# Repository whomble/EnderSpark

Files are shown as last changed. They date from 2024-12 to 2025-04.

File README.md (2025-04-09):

# WireEDM

Wire EDM uses electrical discharges to cut any conductive materials (brass, steel, aluminium even tungsten carbide) with no mechanical forces, enabling high precision, deep cuts, and machining of hard or delicate materials without deformation. 
This project demonstrates how to build a DIY wire EDM machine using salvaged components from an old 3D printer and other affordable parts, keeping the total cost around 250€ + 4 machined parts the ender 3 and less than 50h of work.

The machine's frame and motion system leverage the hardware of the Ender 3,  with 1:51 gear reductions on the X and Y axes to enable extremely slow and precise movements required for EDM. 
A Raspberry Pi Pico clone with a TC4428 and a powerful MOSFET are used to switch up to 10A at 50KHz

This project includes guidance on generating toolpaths using a modified post processor from Fusion 360
Depending on the availability of tools and salvaged materials, replication costs may vary slightly. This project took me a few hundreds of hours of developpment but you should be able to replicate in less than 50h.

The conversion from a 3D printer to a wire EDM can be done in 6 steps:
- Mechanical modifications
- Wire feeder
- Firmware update (marlin)
- Ark generator
- Water loop
- Fusion 360 post processor

The full part list with some product links is in the [parts folder](Parts/)

# WARNiNGS
The voltage is lower than the SELV (50V for AC 120V for DC) in DRY CONDITIONS, for WET CONDITION the SELV is (25V for AC and 60 for DC). In addition there is no GFCI to protect you so disconnect the PSU everytime you're planning to touch a metalic component and wear at leat nitrile gloves. If you don't know precisely what you are doing just skip this project.

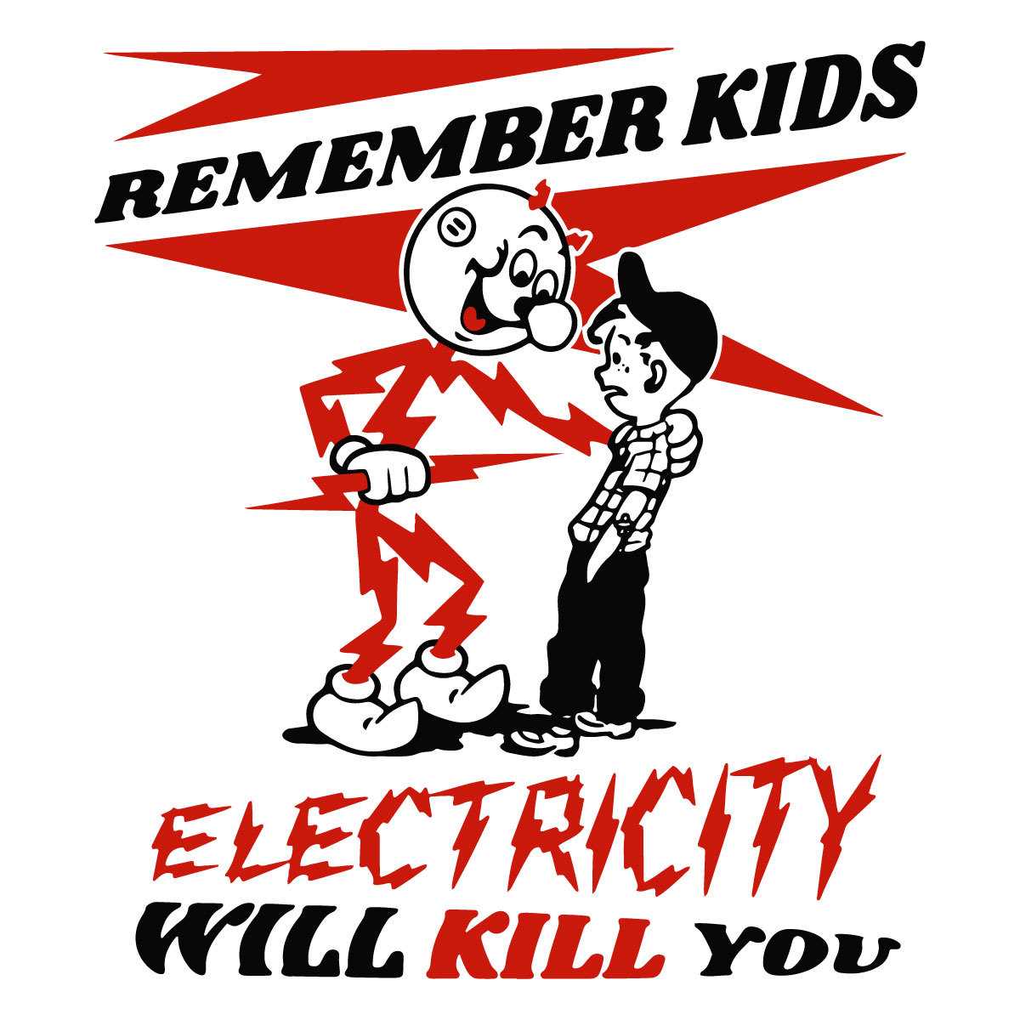
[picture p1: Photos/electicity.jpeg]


Copper is considered as a heavy metal, the best way to deal with the dirty water is to let it sit for a while in a ventilated area to evaporate all the water, after that it's jsut metal powder and can be disposed in the local recycling center.

# Mecanical parts
## Motion

A big advantage of wire EDM compared to CNC milling is that the frame doesn't need to be very stiff, the hardware just need to support the wire feeder on the X axis and the water tank ~4kg on the Y axis. The Z axis isn't used during the cutting process but it's quite usefull to help changing the wire.

I've had a linear rail (MGN12H) on X and Y axis, it can be bolted directly on X axis with T nuts and for the why axis you need to drill 4 holes in the buildplate support thats all.
Wire EDM can be very slow depending on the thickness so one of the most important requirement is to be able to move slowly at a fixed rate. Regular stepper motors aren't able to do that, even with microstepping I made a fully printable belt reducer 1:64 but it need some improvements so I've just brought gearbox for nema 17 that can be directly connected to a 2GT pulley.

## Wire feeder

The wire feeder is the only complicated part which need to be custom made because it needs to fullfill a few requierments:
- Stifness, during the cutting process the arcs can generate vibrations, to achieve a good surface finish the wire need to be very straight
- Electrically insulated, even if the cutting is done under de-ionised water some electrolysis can occur which can reduce the power output. An insulated feeder also prevent from shorts if a metal part fall between the wire and the feeder
- Grounded, at 20kHz the long wire is a big antenna which can emit a lot of parasites and damage electronics. Grounding as much part as possible is crucial to avoid that (and any risk for pacemaker users)
- Tensionner mechanism, to avoid wire vibration the wire need to be adequatly tensionned.
- Waste spool, wire edm consume the workpiece AND the wire, depending on the material it can use a lot of wire
- Hard wire guide, I you have an old ender 3 you've probably experience filament grinding the extruder even if its plastic against plastic, the same thing can happend here with soft brass

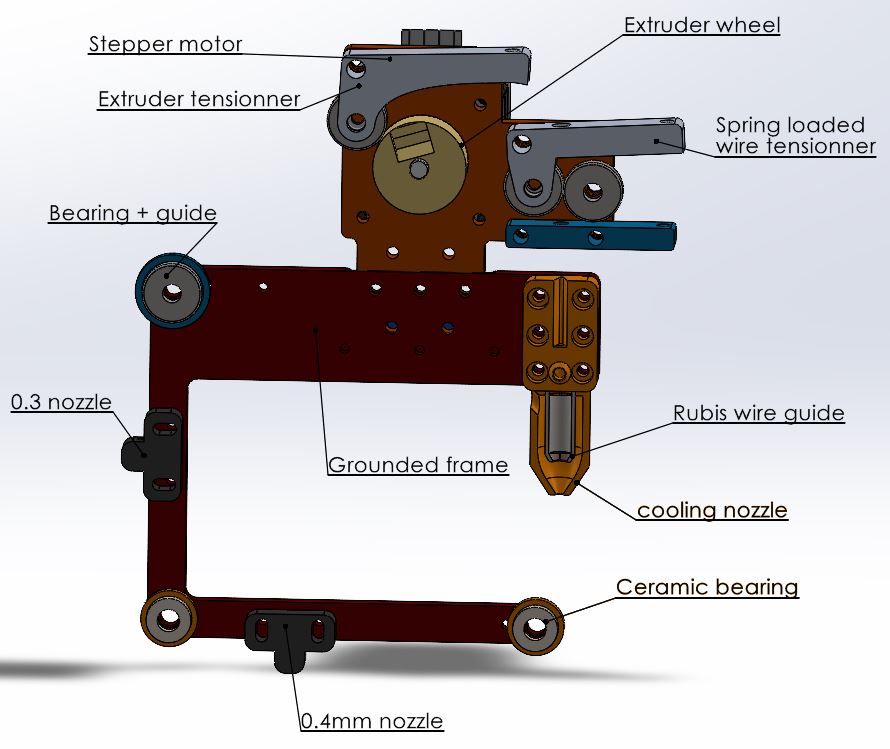
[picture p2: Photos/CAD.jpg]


This is the CAD of the second version, the extruder (nema 17 + a brass cylinder) is pulling the wire all the way from the tensionner. 
The tensionner conssit of two all bearing pressing into each other like a 3D printer extruder, the sping can b adjust to block more the wire and provide more tension.
Then, the wire need to be guided very precisely, for the upper guide I use a off the shelf rubis nozzle with a plastic nozzle around it for watercooling. The lower guide is a ceramic ball bearing with a PLA spacer and a .4mm brass nozzle to push the wire against the spacer. The two other ball bearings (ceramic for the lower one and steel with plastic cover for the upper one) just guide the wire to the extruder.

The ball bearings needs to be in ceramic for three reason:
1. Corosion
2. No lubricant can desovle in water
3. High hardness

The wire is connected to the (-) terminal of the PSU by the brass wheel and in the future a tungsten carbide contact block, but since the wire emit EMF like an antenna, I want to ground as much metal as I can, so the whole motor assembly is at the same potential as the wire, but the frame of the printer and the red part are grounded. The voltage arent high so a layer of epoxy or an anodization is enougth to insulate the two regions.

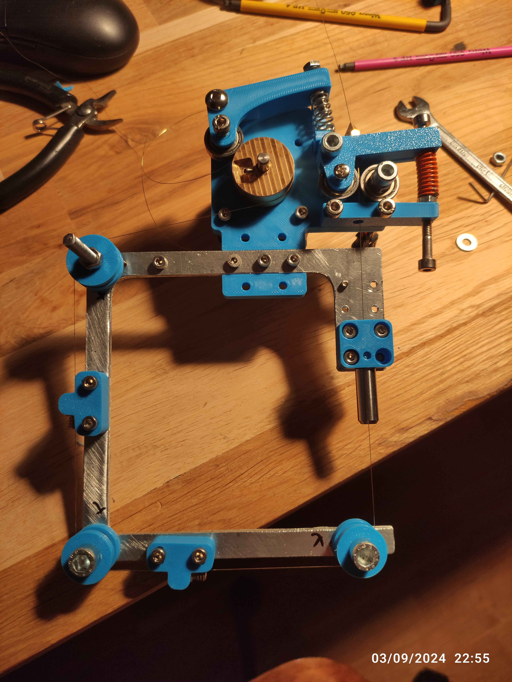
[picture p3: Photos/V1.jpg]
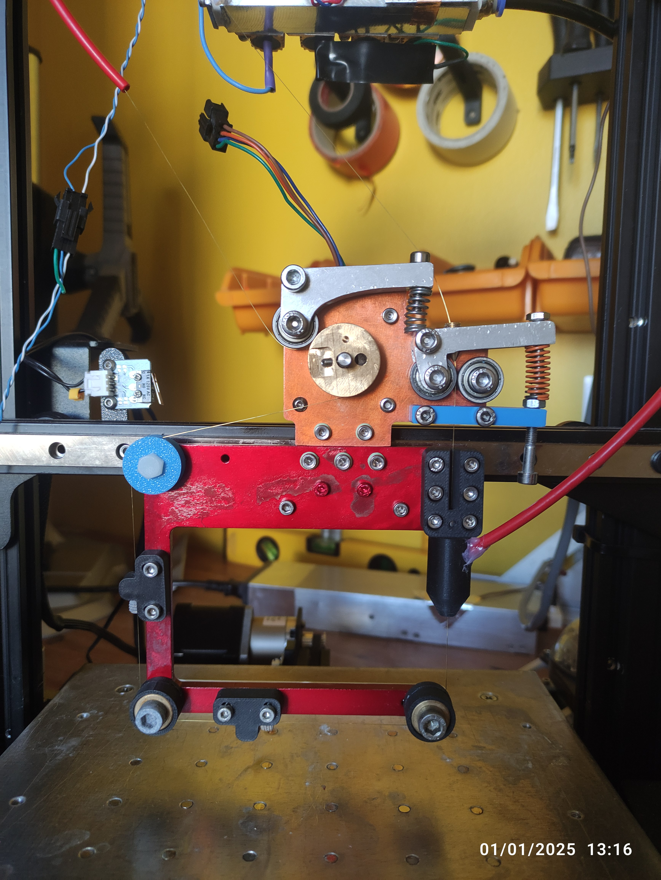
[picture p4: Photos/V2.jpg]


The first version on the left use a lots of printed parts, it works but the tensionner some part can flex and reduce the wire tension/straightness so I made a second version in 5mm thick alluminium plate with 10mm thick tensionners.

All the parts are availlable in .sldprt and .step

### Manufcaturing

Both the red and orange parts are 5mm thick aluminium cutted with my homemade CNC with a 3.175mm single flute endmill, the geometry is a bit complex and can be improve but if you want to make it there is a catch. The two parts are electrically insulated and need to be very straight, there is two options for insulating metalic coating. 
- Anodisation of aluminium + galvanic varnish, it requier sulfuric acid and other chemicals and it's not that easy to make a thick and strong coating
- Powder coating, there's a few hobbist projects but it involve fine powder which isn't better than sulfuric acid.

Both can be DIY or manufacturer by a chinese company like pcbway or whatever, in the case of powder coating, the frame can be made out of steel (not stainless) wich will give way more stifness. 

The two other aluminium parts doesn't need any coating same for the brass wheel, it's just a cylinder with 3 holes.

### Spool

Wire edm as you can guess consume wire, so I need a simple way to manage the waste wire. My solution is to have the new spool of wireconnected to the waste spool with magnet so the second one can be drived by the first one. Since the first spool will get smaller and smaller and the second bigger and bigger, the first one will have to turn way fater to maintain a tension. With this configurtion, the first spool has a way smaller inner diameter which made it spin fzster at any moment. The magnets act like a clutch to maintain constant load at variable speeds.

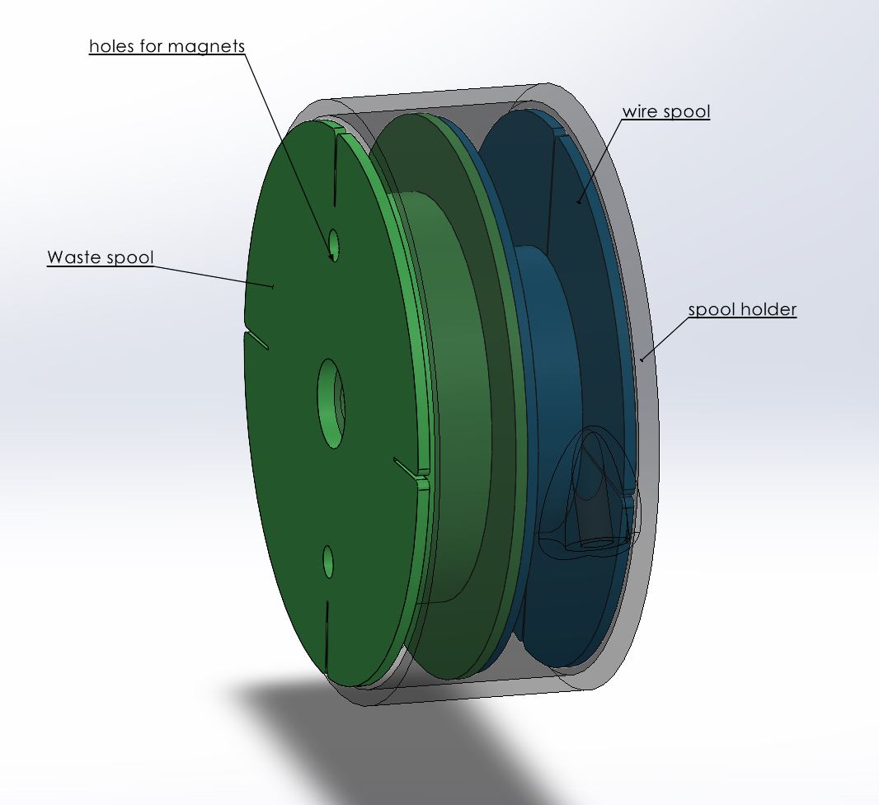
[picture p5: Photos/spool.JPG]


# Electronics
## generator

It's actually pretty easy to make an arc for EDM, it won't be as powerfull as a commercial machine but pretty close. We just need to switch a powerfull MOSFET on and of very fast, I use the IRF135B203 wich can handle 135V 129A and 500A peak. The mosfet is drived by a TC4428 with a schotcky diode to protect the IC a square pwm signal is generated by the pi pico, the pico code is optimised to generate the wave as fast as possible.



## Power managment 

The power supply should be able to deliver at least 5A, 48V is enougth to cutt alluminium but a higher voltager means a higher energy stored in the capacitors (E = 1/2C U²). If you plan to cut copper or steel you can buy a switch mode power supply with adjustable output (mine can go up to 110V).

In the best case scenario, each pulse will create an arc and remove some matter but in realitty sometimes the wire is too far to create a spark and sometimes the wir eis in direct contact and will create a (momentary) short circuit. In the future I will make a short circuit detection system but for now a serie of 100W what resistors limit the current to avoid destroing the PSU and the wire.

Last part is the capacitors, it helps deliver high current durring short amount of time. You can't use some standard electrolitic capacitor (belive me I tried) ceramic is a good option but we need very low ESR so polymer is the only suitable option. In my setup I use 4x 4.7uF in parallel so ~20uF rated for 200V.

These 3 main components are connected to a waterblock for cooling, in my experience it's a bit overkilled and air cooling will be enougth in the future but I need to circulate the water anyway so...

# Water

The EDM process must be done under a dielectric fluid, it can be ethanol, oil or kerosene but the easyest solution is obviously deionised water. Water is also used for cooling (the electrical components and the workpiece) and chip evacuation. The "builtplate" is a water tank made out of acrily sheets welded with aceton and a bit of silicone for etancheity. I've also add a steel shit so I can quickly remove it from my magnetic buildplate.

EDM generate a ton of small metalic particles which needs to be filter during the cutting, The best pump I've found is a membrane pump which can provide high pressure (necessary for good filtration) and is quite silent when underpowered, it's design for 24V and I power it between 5-7V depending on the material. The filter is a standard polyester coton filter <0.1um in a cardrige in the future I'll probably try washables filters like ceramic or stainless steel. I use push pull and 6mm tubes for all my connection except for the nozzle its a 4mm.

After each cuts I put the deionised water in it's original tank for decantation, and separate the "pure" water from the dirty one a few days later.

Copper is consiered as a heavy metal, the best way to deal with the dirty water is to let it sit for a while in a ventilated area to evaporate all the water, after that it's jsut metal powder and can be disposed in the local recycling center.

# Firmware modifications

# Toolpath generation

The two easiest ways to generate a gcode is with a slicer or with a cam plugin. I've tried kirimoto which have a wire edm mode but there's very little features and you can't control the extruder. I've also tried cura, the limitation is that you can't set a very small speed, I even tried modifiyng the software but I coulnd'nt find a solution, maybe with orca slicer?

In my opinion the easyest solution is to use the CAM part of fusion 360 with the laser/waterjet mod. 



It's easy to setup a waterjet tool with 0.3mm stream and you can add a very long lead in to enter the workpiece from anywhere. You don't have to worry about feeds and speeds here, you just need to set all the hight to zero to avoid Z movements, and set up the appropriate thickness.

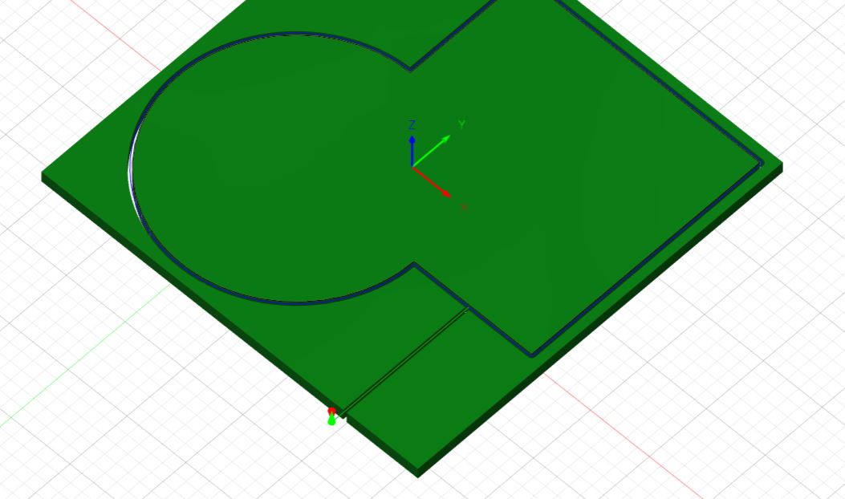
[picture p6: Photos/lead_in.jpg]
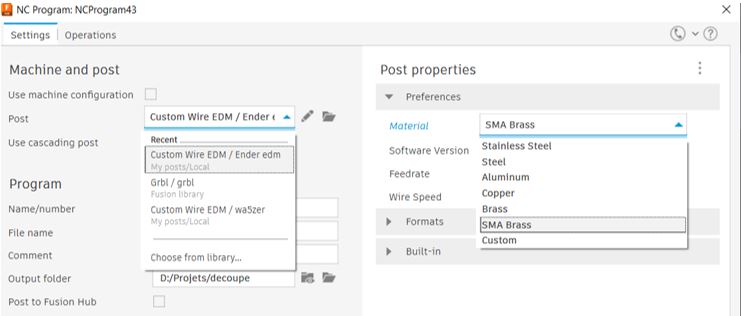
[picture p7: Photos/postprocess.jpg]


Then you need to select the wire edm post processor, I modified the wazer post processor to match my needs, I will not detail it here, the file is in this folder, you just have to paste it in the appropriate location.

I have a very small database for differents materials, so if the thickness is right, just selec the material and it should be good to go. It's an ongoing project soyou will probably have sligly differents settings than me, I'll recommand you to do a speedtest for the material you're planing to cut and modify the database:

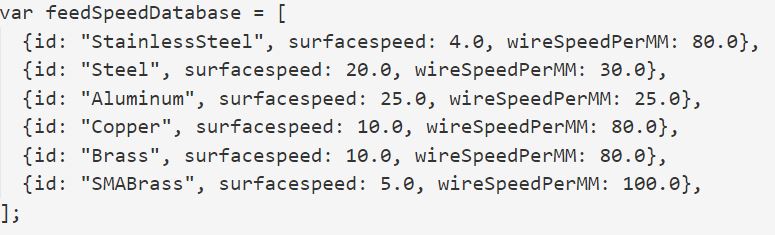
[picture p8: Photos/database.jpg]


surfacespeed is the speed in mm²/min, which correspond to the linear speed for a defined thickness ex: 3mm/min for 10mm thick aluminium is 30mm²/min.
wirespeedpermm is the wire consumed per mm² with the previous example of 30mm²/min and 25mm it will consume 750mm of wire to cut this amount of material in 1min.

A cheap 100m of 0.2mm joaillery brass wire (2€) will last for more than two hours ~0.02€/m, a more expensive 5kg of edm 0.25mm brass wire (110€) is almost 12km so ~0.01€/m and 250h of use.
In the future I will try molybdenum wire which is just a bit more expensive but it can be used several times but I need to design a back and forth drive.

Some more commun supply are also needed like heat shrink tube, solder, wires (I use wires from old RJ45 cable it can handle something like 5A without a problem, its free nd easly accessible).

A lots of tools are needed to work properly:

- Soldering iron
- Drill press
- Caliper
- Dial indicator
- Heat gun
- A good square rule
- Handed metal saw 
- Metal band saw (if your alumiun extrusions needed to be with a perfect 90° angle)
- Hand drill
- Center punch
- Marker for metal
- Hammer, clamps, screw drivers others hand tools
- 3D printer
- deburr tool

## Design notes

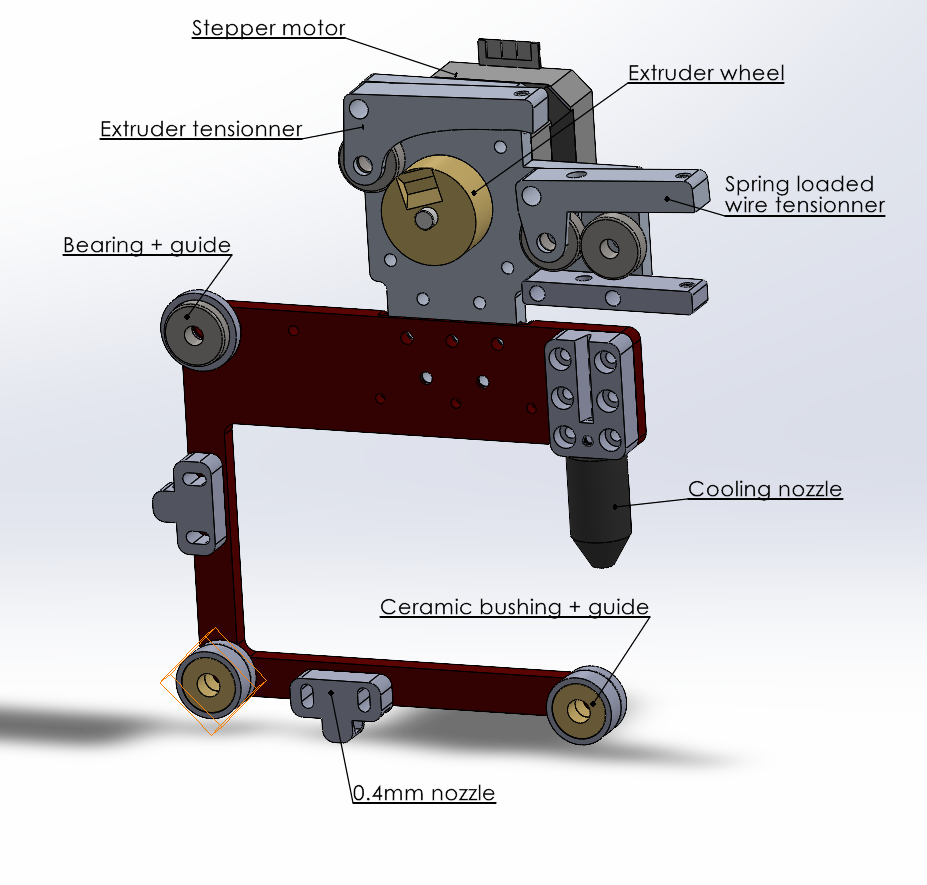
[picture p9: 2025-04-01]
Photos/wirefeeder.png

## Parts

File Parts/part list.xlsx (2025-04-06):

Raspberry pi pico | 1 | 5.0 € | 5 € | https://fr.aliexpress.com/item/1005008244091735.html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
Linear rail MGN12H 300mm | 2 | 12.0 € | 24 € | https://fr.aliexpress.com/item/1005003696820721.html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
M3*8 screws | 50 | 2.0 € | 2 € | https://fr.aliexpress.com/item/32810872544.html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
M3 T nuts | 20 | 3.0 € | 0 € | https://fr.aliexpress.com/item/32788058829.html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
M5*16 screws | 8 | 2.0 € | 2 € | https://fr.aliexpress.com/item/1005005879037174.html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
M6*12 screws | 2 | 3.0 € | 6 €
M4*12 screws | 5 | 2.0 € | 10 €
Nema 17 gearbox 1:51 | 2 | 20.0 € | 40 € | https://fr.aliexpress.com/item/1005008063969593.html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
24V membrane pump | 1 | 15.0 € | 15 € | https://fr.aliexpress.com/item/1005008493661821.html?scm_id=1007.40050.354490.0&scm-url=1007.40050.354490.0
Filter cardridge | 4 | 2.0 € | 8 € | https://fr.aliexpress.com/item/1005006706760484.html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
Filter holder | 1 | 15.0 € | 15 € | https://fr.aliexpress.com/item/1005007179471330.html?scm_id=1007.40050.354490.0&scm-url=1007.40050.354490.0
Adapter 1/2-> 6mm | 2 | 2.0 € | 4 € | https://fr.aliexpress.com/item/1005002505807954.html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
Adapter m6-> 6mm | 5 | 1.0 € | 5 €
6mm pneumatic pipes (2m) | 1 | 2.5 € | 2.5 € | https://fr.aliexpress.com/item/1005005444191688.html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
Waterblock | 1 | 8.0 € | 8 € | https://fr.aliexpress.com/item/1005004478886659.html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
TC4428 | 2 | 2.0 € | 4 € | https://fr.aliexpress.com/item/1005006912580387.html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
IRF135B203 (or similar) | 2 | 5.0 € | 10 €
4.7uF polymer capacitor | 10 | 0.8 € | 8 € | https://fr.aliexpress.com/item/1005008476927781.html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
Buck converter | 1 | 2.0 € | 2 € | https://fr.aliexpress.com/item/1005001711248152.html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
Acrylic sheet (3*235*635mm) | 1 | 20.0 € | 20 € | hardware store
Oled screen | 1 | 2.5 € | 2.5 € | https://fr.aliexpress.com/item/1005004355547926.html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
L7812CV | 1 | 2.0 € | 2 € | https://fr.aliexpress.com/item/1005007531573602.html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
JST connectors | 1 | 3.0 € | 3 € | https://fr.aliexpress.com/item/1005006498660940.html?scm_id=1007.40050.354490.0&scm-url=1007.40050.354490.0
Banana connectors | 1 | 1.5 € | 1.5 € | https://fr.aliexpress.com/item/1005006400659486.html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
Wire diodes resistor | 1 | 5.0 € | 5 €
Ceramic bearings | 2 | 6.0 € | 12 € | https://fr.aliexpress.com/item/1005008350254851.html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
Bearings | 4 | 0.0 € | 0 € | from ender3 rubber wheels
PLA ~200g | 1 | 4.0 € | 4 €
Ender3 | 1 | 0.0 € | 0 €
 |  | Total | 220.5 €
0,2mm brass wire (100m) | 5 | 2.0 € | 10 € | https://fr.aliexpress.com/item/1005006203319769.html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
0,25mm brass wire (5kg) | 1 | 110.0 € | 110 € | https://fr.aliexpress.com/item/1005006169662498.html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
0,18 molybdenum wire (2km) | 1 | 40.0 € | 40 € | https://fr.aliexpress.com/item/1005008417132381.html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

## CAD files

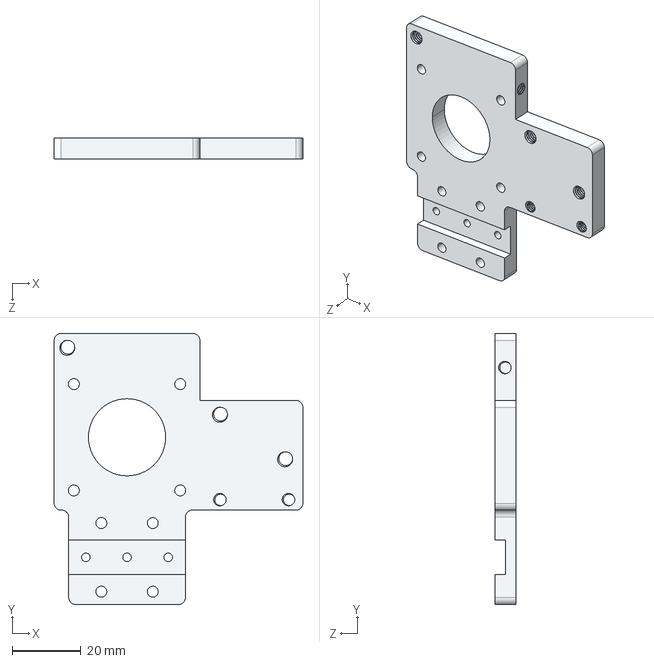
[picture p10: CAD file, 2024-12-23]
step_files/extruder mount.STEP
72.5 x 79.0 x 6.00 mm

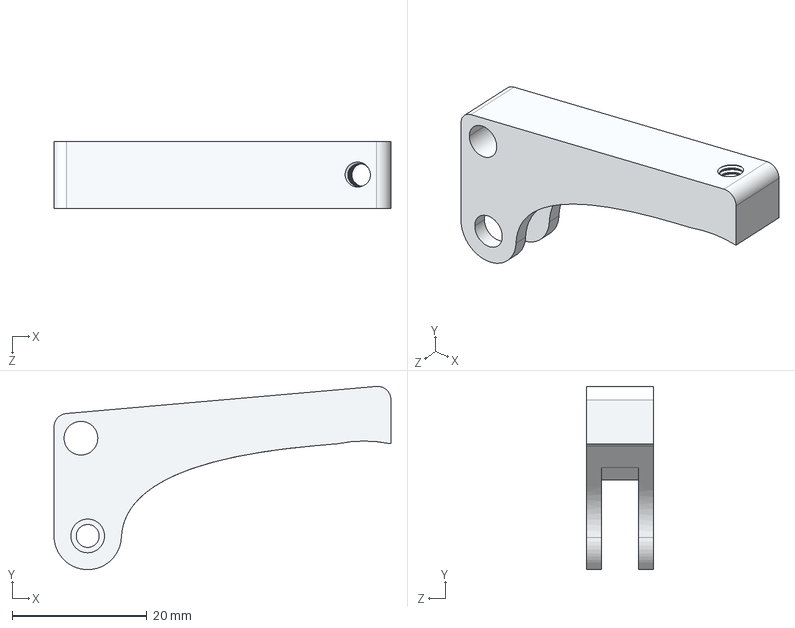
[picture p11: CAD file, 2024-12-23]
step_files/extruder tensioner.STEP
50.0 x 27.2 x 10.0 mm

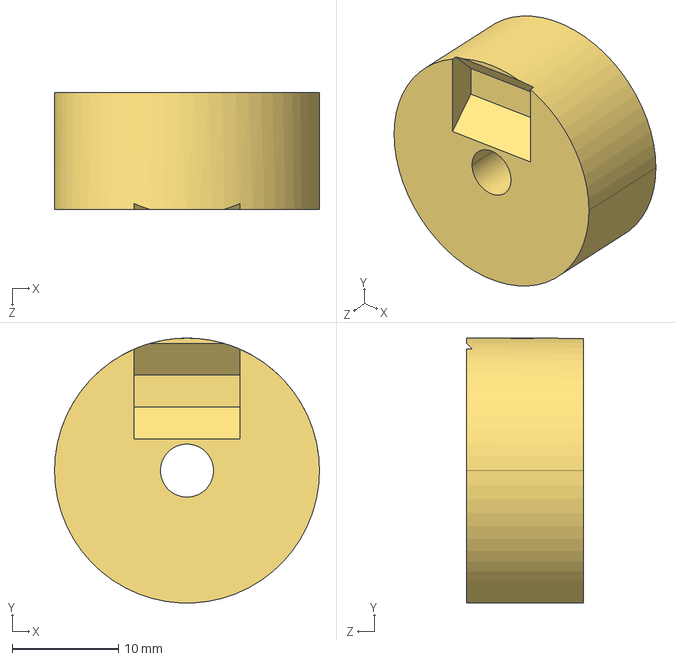
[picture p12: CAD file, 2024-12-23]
step_files/brass wheel.STEP
25.0 x 25.0 x 11.0 mm

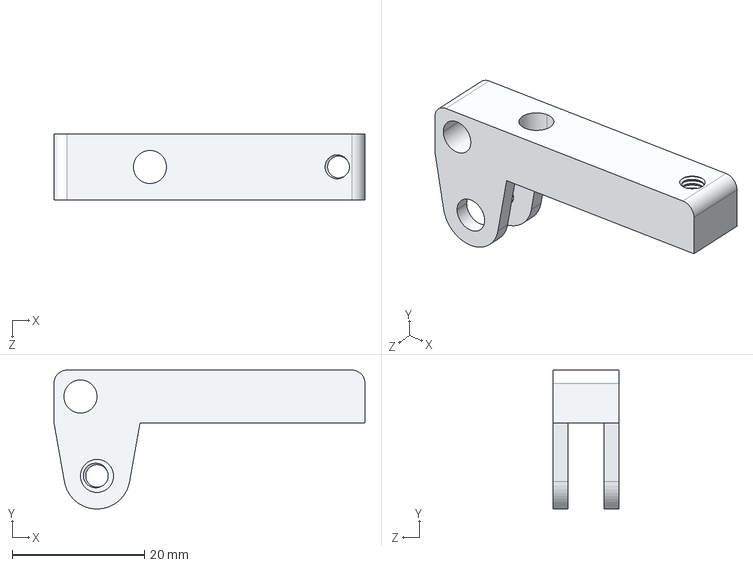
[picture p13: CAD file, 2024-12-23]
step_files/wire tensionner.STEP
47.0 x 21.0 x 10.0 mm

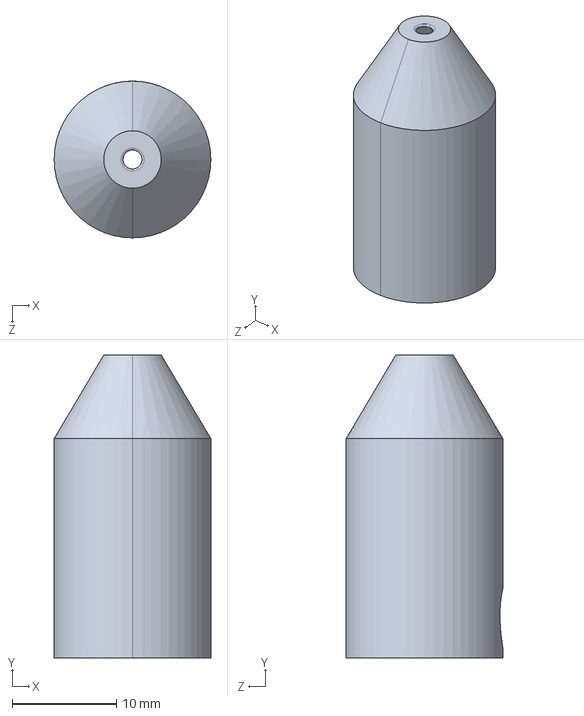
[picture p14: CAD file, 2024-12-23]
step_files/water_nozzle.STEP
15.0 x 29.0 x 15.0 mm

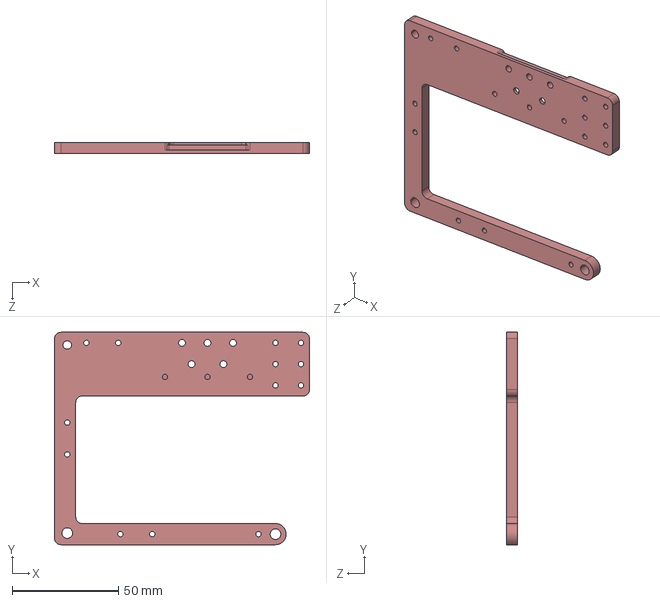
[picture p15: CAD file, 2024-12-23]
step_files/Aluminium structure.STEP
120.0 x 100.0 x 5.00 mm
